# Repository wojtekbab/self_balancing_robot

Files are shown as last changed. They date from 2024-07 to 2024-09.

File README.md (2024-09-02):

# Two-Wheeled Balancing Robot Project

## Overview
Repository contains code for microcontroller ESP-32 with implemented control system with LQR regulator. Microcontroller connects to local network and acts like a web server, providing GUI on website to control vehicle. Matlab scripts were used to calculate mathematical model and simulink system was designed to veryficate close loop system. 

## Table of Contents
1. [ESP32 Code](#esp32-code)
2. [MATLAB Code](#matlab-code)
3. [Inventor Project](#inventor-project)
4. [KiCad Project](#kicad-project)

## ESP32 Code
Code was written in PlatformIO extension with arduino framework. FreeRTOS was used with hardware interrupts and tasks for:
- service encoders
- measure imu data
- filter data with Kalman Filter
- calculate rest of state variables
- generate reference vector
- calculate control for motors
- log data 

### Files
- `main.cpp`: main file for the ESP32.
- `defines.cpp`: file with defines.
- `globals.cpp`: file with global variables used by tasks.
- `interrupts.cpp`: interrupts service routines.
- `utilities.cpp`: some utility functions.
- `tasks.cpp`: file with FreeRTOS tasks.
- `web_server.cpp`: web server with html page.
- `platformio.ini`: configuration file used by PlatformIO extension.

### How to Run
1. Create empty project with PlatformIO.
2. Copy `platformio.ini` file into project.
3. Copy header and source files into folder src.

## MATLAB Code
The MATLAB code is used to calculate mathematical model and simulate system.

### Files
- `s1_parameters.m`: script with system parameters.
- `s2_mathematical_model.m`: script for calculate unlinear and linear model as state-space matrixes.
- `sim1_unlinear_model_with_LQR.slx`: simulink close loop system with LQR regulator 

### How to Run
1. Open Matlab 2023b.
2. Run `s2_mathematical_model.m` to load parameters and calculate K matrix.
3. Run `sim1_unlinear_model_with_LQR.slx` to test system output for given reference velocities or different initial state.

## Python Code
In case when Matlab is not available, all necessary scripts were translated for python.

### Files
- `requirements.txt`: contain all necessary python modules.
- `parameters.py`: contain dictionary with system parameters.
- `p1_mathematical_model.ipynb`: notebook for symbolic equations with sympy to obtain mathematical model.
- `p2_closed_loop_system.ipynb`: notebook to make simulations with closed loop system with LQR regulator  

### How to Run
1. Install necessary modules.
2. Run `p1_mathematical_model.ipynb` to obtain mathematical model.
3. Run `p2_closed_loop_system.ipynb` to see result of system simulations.

## Inventor Project
Image from Inventor project was included to repository. 3D model was created to design distribution of elements and to calculate parameters of vehicle inertia. 

### Images
<div align="left">
<p>
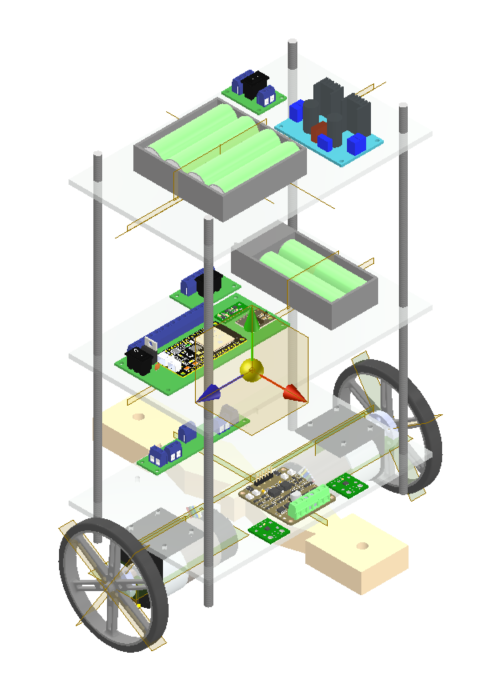
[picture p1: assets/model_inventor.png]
Inventor Assembly
    
    Real model
</p>
    <p><em>Figure 1: 3D model from Autodesk Inventor and real model.</em></p>
</div>

## KiCad Project
Images from KiCad project was included to repository. PCB board was created for electronic parts from system to avoid EMI interferences from DC motors.

### Images
<div align="left">
<p>
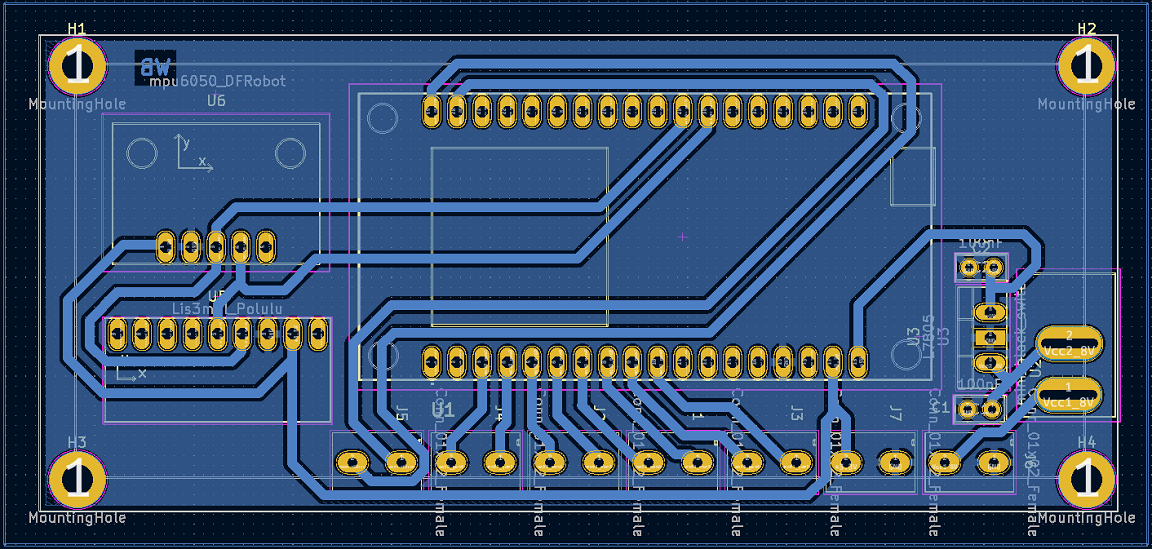
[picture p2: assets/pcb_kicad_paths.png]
    
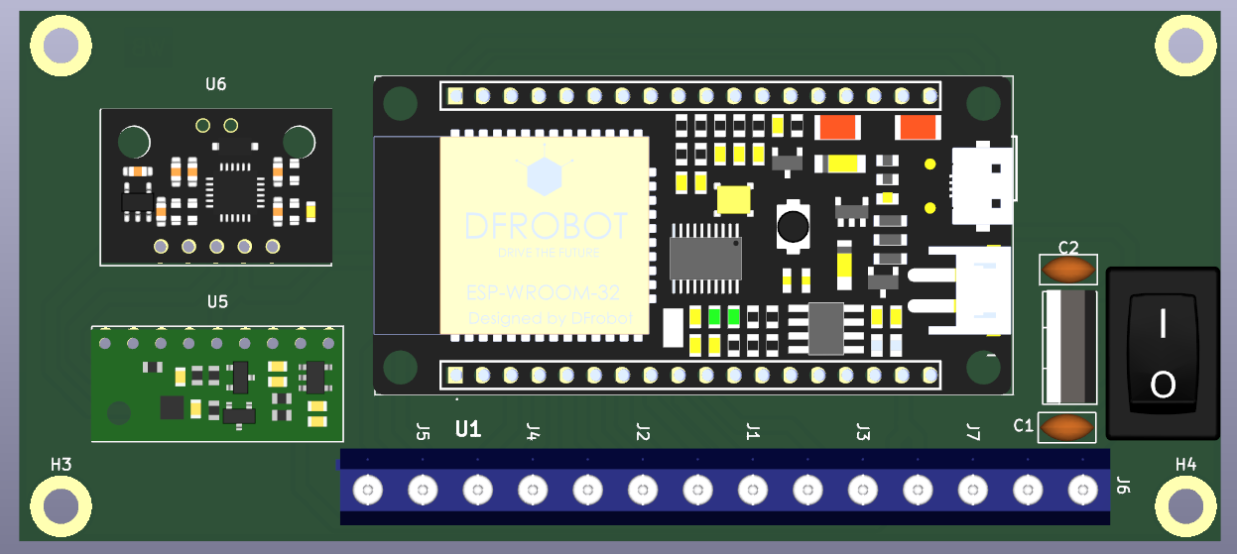
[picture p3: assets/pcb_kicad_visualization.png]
    
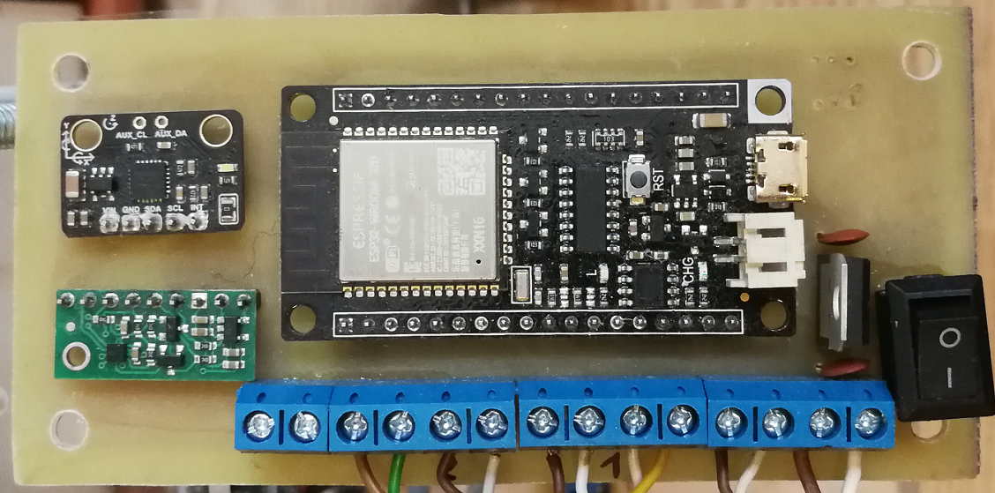
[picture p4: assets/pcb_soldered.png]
    
</p>
    <p><em>Figure 2: designed paths, visualization, home made board</em></p>
</div>

## Demo

<p>
  Link to demo video:
  <a href="https://www.youtube.com/watch?v=7iqSqyg-NeA" >https://www.youtube.com/watch?v=7iqSqyg-NeA</a>
</p>

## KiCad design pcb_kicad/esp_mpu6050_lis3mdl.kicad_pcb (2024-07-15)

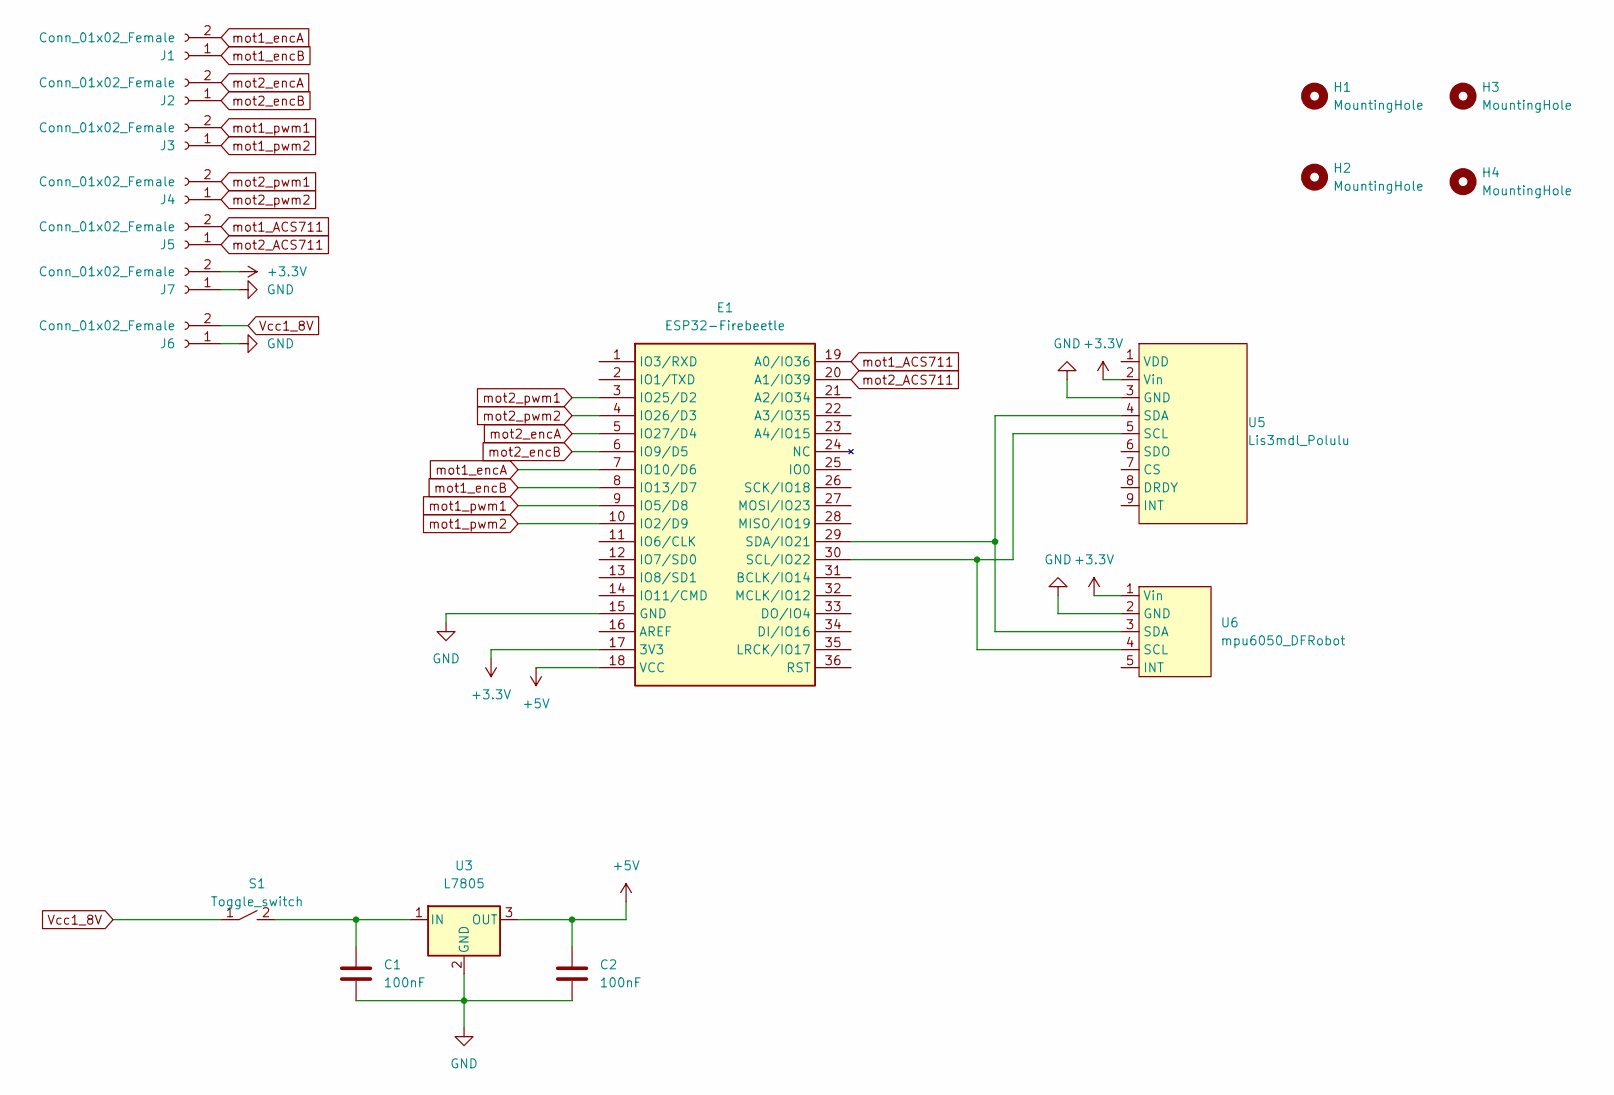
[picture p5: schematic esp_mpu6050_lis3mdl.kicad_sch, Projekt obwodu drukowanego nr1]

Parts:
C1, C2: 100nF; C_Disc_D5.0mm_W2.5mm_P2.50mm
E1: ESP32-Firebeetle; FIREBEETLE_ESP32
H1, H2, H3, H4: MountingHole; MountingHole_3.2mm_M3_DIN965_Pad
J1, J2, J3, J4, J5, J6, J7: Conn_01x02_Female; zlacze ARK_2
S1: Toggle_switch; mini_black_switch
U3: L7805; LM78xx
U5: Lis3mdl_Polulu; lis3mdl_Pololu
U6: mpu6050_DFRobot

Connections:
+3.3V: E1.17 (3V3), J7.2, U5.2 (Vin), U6.1 (Vin)
+5V: C2.1, E1.18 (VCC), U3.3 (OUT)
GND: C1.2, C2.2, E1.15 (GND), J6.1, J7.1, U3.2 (GND), U5.3 (GND), U6.2 (GND)
unnamed: C1.1, S1.2, U3.1 (IN)
unnamed: E1.29 (SDA/IO21), U5.4 (SDA), U6.3 (SDA)
unnamed: E1.30 (SCL/IO22), U5.5 (SCL), U6.4 (SCL)
Vcc1_8V: J6.2, S1.1
mot1_ACS711: E1.19 (A0/IO36), J5.2
mot1_encA: E1.7 (IO10/D6), J1.2
mot1_encB: E1.8 (IO13/D7), J1.1
mot1_pwm1: E1.9 (IO5/D8), J3.2
mot1_pwm2: E1.10 (IO2/D9), J3.1
mot2_ACS711: E1.20 (A1/IO39), J5.1
mot2_encA: E1.5 (IO27/D4), J2.2
mot2_encB: E1.6 (IO9/D5), J2.1
mot2_pwm1: E1.3 (IO25/D2), J4.2
mot2_pwm2: E1.4 (IO26/D3), J4.1

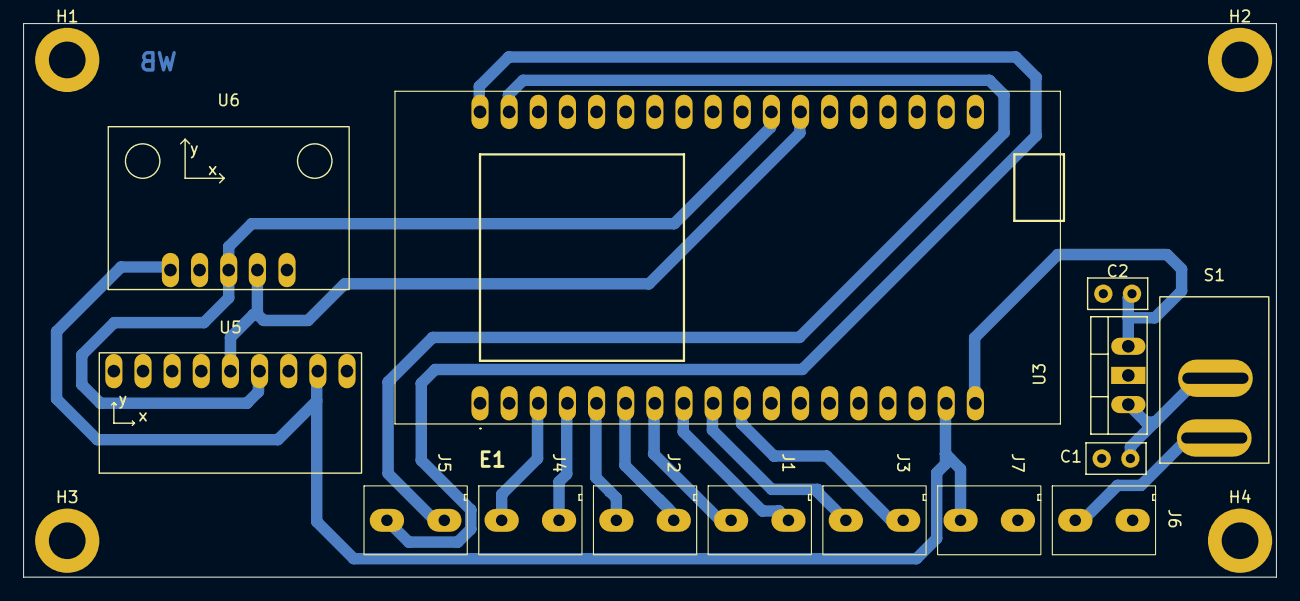
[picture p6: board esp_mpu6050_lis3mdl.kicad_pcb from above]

Board: 2 copper layers, 109.2 x 48.3 mm, 18 parts (0 on the bottom side), 17 nets.

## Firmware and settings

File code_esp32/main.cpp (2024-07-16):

/**
 * @file main.cpp
 * @author Wojciech Babicki (wojciech.babicki@op.pl)
 * @brief
 * @version 0.1
 * @date 2024-07-15
 *
 * @copyright Copyright (c) 2024
 *
 */
#include "defines.hpp"
#include "globals.hpp"
#include "tasks.hpp"
#include "web_server.hpp"
#include "interrupts.hpp"
#include "utilities.hpp"

/**
 * @brief function initialize serial, set interrupts, initialize FreeRTOS objects, connect to wifi, initialize tasks
 *
 */
void setup(void)
{
  // serial
  Serial.begin(115200);
  while (!Serial)
  {
    delay(10);
  }
  Serial.println("Serial initialized!");

  // interrupts
  pinMode(GPIO_MOT1_ENCA, INPUT_PULLUP);
  pinMode(GPIO_MOT1_ENCB, INPUT_PULLUP);
  pinMode(GPIO_MOT2_ENCA, INPUT_PULLUP);
  pinMode(GPIO_MOT2_ENCB, INPUT_PULLUP);

  attachInterrupt(GPIO_MOT1_ENCA, ISR_callback_mot1, CHANGE);
  attachInterrupt(GPIO_MOT1_ENCB, ISR_callback_mot1, CHANGE);
  attachInterrupt(GPIO_MOT2_ENCA, ISR_callback_mot2, CHANGE);
  attachInterrupt(GPIO_MOT2_ENCB, ISR_callback_mot2, CHANGE);

  // FreeRTOS objects
  mutex_state_variables = xSemaphoreCreateMutex();
  mutex_reference_variables = xSemaphoreCreateMutex();
  mutex_mpu_measurement = xSemaphoreCreateMutex();
  mutex_control_values = xSemaphoreCreateMutex();
  queue_reference_velocities = xQueueCreate(QUEUE_JOYSTICK_LENGTH, sizeof(Reference_velocities_struct));
  semaphore_mpu_initialized = xSemaphoreCreateBinary();
  xEventGroup = xEventGroupCreate();

  // wifi
  WiFi.begin(ssid, password);
  while (WiFi.status() != WL_CONNECTED)
  {
    delay(1000);
    Serial.println("Connecting to WiFi..");
  }
  Serial.println("Connected to WiFi");
  Serial.println(WiFi.localIP());

  // server
  setupWebServer();

  // tasks
  Serial.println("Initializing tasks...");
  xTaskCreatePinnedToCore(mpu_measurement_task, "mpu_measurement_task", 4096, NULL, 2, NULL, app_cpu);
  xSemaphoreTake(semaphore_mpu_initialized, portMAX_DELAY);
  xTaskCreatePinnedToCore(theta_obs_task, "theta_obs_task", 4096, NULL, 3, NULL, app_cpu);
  xTaskCreatePinnedToCore(x_psi_obs_task, "x_psi_obs_task", 4096, NULL, 1, NULL, app_cpu);
  xTaskCreatePinnedToCore(reference_task, "reference_task", 2048, NULL, 1, NULL, app_cpu);
  xTaskCreatePinnedToCore(motors_task, "motors_task", 4096, NULL, 4, NULL, app_cpu);
  xTaskCreatePinnedToCore(printing_task, "printing_task", 4096, NULL, 5, NULL, app_cpu);

  Serial.println("All tasks initalized");
  delay(500);
}

/**
 * @brief function contains only non-block delay to avoid problem with watchdog timer
 *
 */
void loop()
{
  vTaskDelay(1000 / portTICK_PERIOD_MS);
}

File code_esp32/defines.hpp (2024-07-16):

/**
 * @file defines.hpp
 * @author Wojciech Babicki (wojciech.babicki@op.pl)
 * @brief 
 * @version 0.1
 * @date 2024-07-15
 * 
 * @copyright Copyright (c) 2024
 * 
 */
#ifndef DEFINES_HPP
#define DEFINES_HPP

#include <freertos/FreeRTOS.h> 

// encoder pins
#define GPIO_MOT1_ENCA 10
#define GPIO_MOT1_ENCB 13
#define GPIO_MOT2_ENCA 27
#define GPIO_MOT2_ENCB 9

// pwm pins for control motors
#define GPIO_MOT1_PWM_R 5
#define GPIO_MOT1_PWM_L 2
#define GPIO_MOT2_PWM_R 25
#define GPIO_MOT2_PWM_L 26

// max references for html page control
#define REFERENCE_X_DOT_MAX 0.5f
#define REFERENCE_PSI_DOT_MAX 1.57f

// queue length (used for data from html page) 
#define QUEUE_JOYSTICK_LENGTH 1

// use core 1 for user program
#if CONFIG_FREERTOS_UNICORE
static const BaseType_t app_cpu = 0;
#else
static const BaseType_t app_cpu = 1;
#endif

// for group event
#define START_STOP_BIT (1 << 0)

#endif // DEFINES_HPP
